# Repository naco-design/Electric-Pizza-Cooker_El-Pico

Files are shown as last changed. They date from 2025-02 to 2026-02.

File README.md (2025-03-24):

# Electric Pizza Cooker El-Pico
El-Pico, This is a programmable Electric Pizza Cooker (Oven)!
\
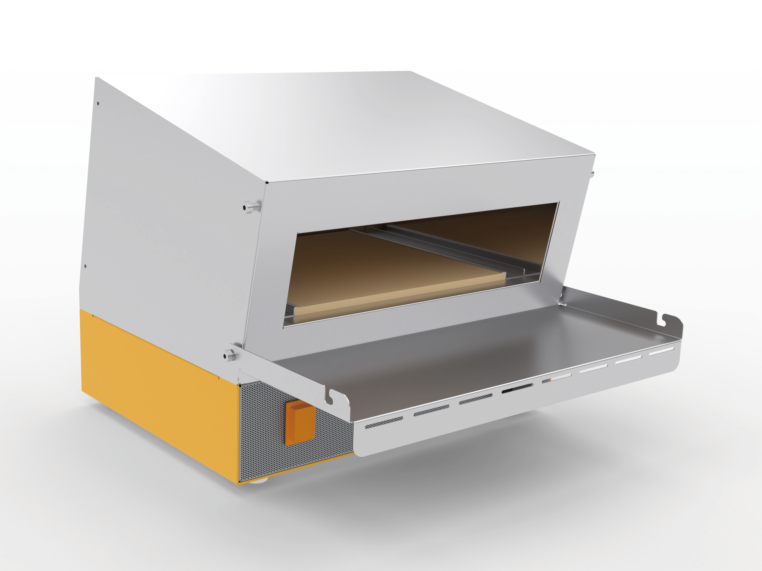
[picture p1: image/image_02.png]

CADデータのレンダリングイメージ

## Why Pizza ?
おいしいピッツァを食べたい！→ピザ窯をつくろう
\
\
以下のデータを順次公開します。
* 板金用STEPファイル
* 3Dプリント用STLファイル
* ファームウェア
* 部品のリスト
* 配線や組み立ての手順
* レシピ

## 開発にあたって
* おいしいピッツァが焼けること
* 日本の家庭用コンセントで使えること（AC100V 15A以内）
* 窯の天井485℃以上、炉床380~430℃で90秒以内で焼成可能を目指す

## 実機写真
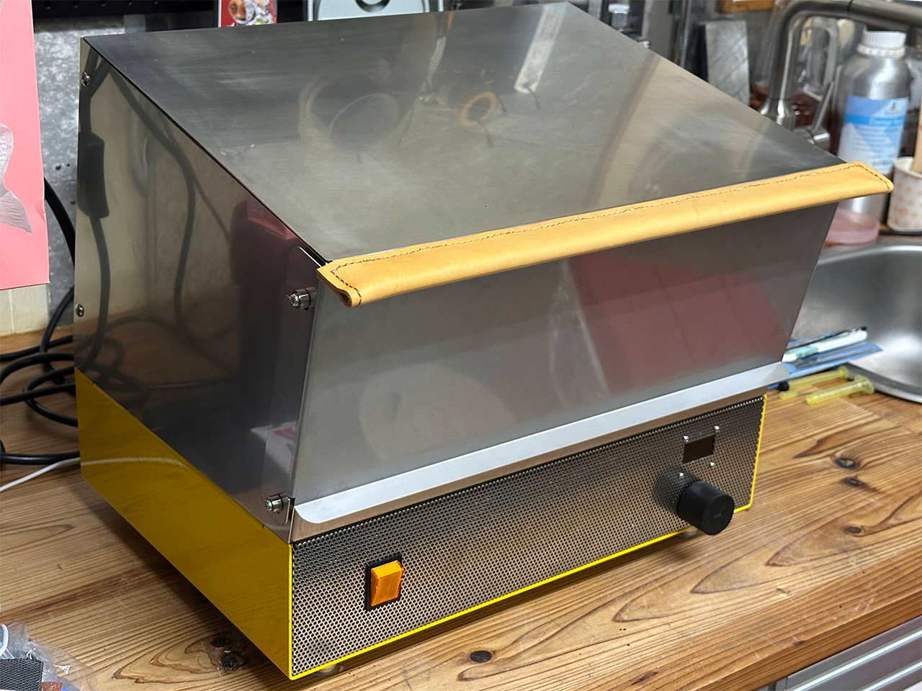
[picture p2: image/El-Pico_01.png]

天井500℃、炉床420℃の設定で90秒の焼成でおいしいピッツァを焼くことが出来ました。


2025/03/23開催のNT京都にて実機の展示
チルドピザを天井500℃、炉床370℃の設定で90秒の焼成


## コンセプト
### もっと多くの人を笑顔にしたい
開発のきっかけは、学園祭での飲食ブースの混雑と[Xの@SteveKasuya2さんのポスト](https://x.com/SteveKasuya2/status/1695339494550224910)でのオーブントースター改造ピザ窯で90 秒でピザを焼きあげる様子から、素早い提供を行えるマシンの開発に魅力を感じたことでした。
さらに、震災の報道で見た避難所の様子と[@nanbuwksさんの災害支援でピザ窯で炊き出しの記事](https://qiita.com/nanbuwks/items/adf3fea1b13d262047f9)にある支援活動の情報から、電気式のピザ窯の有用性を感じたのも理由です。

### 食は心身の健康の増進と豊かな人間形成に資する
2005 年には食育基本法が施行され、食育が現在及び将来にわたる健康で文化的な国民の生活と豊かで活力ある社会の実現に寄与するものであること、[SDGｓとも深くつながること](https://www.maff.go.jp/j/syokuiku/network/topics/2022forum.html)、また、生活の中で身近に体験する科学であり、結果をすぐに体感出来ることや新たな創意工夫を発想しやすいことから、プログラム可能なピザ窯開発を教材化しようと考えました。

### 新たな可能性は改良から生まれます。
公開するプログラムや設計を改良することで、新たな料理や素材に合わせた設定を探ったり、より良い制御を試すことが出来ます。\
筐体を作り変えたり、断熱材や蓄熱材、遮熱処理などを変更するとどうなるか、より使いやすくするためのアイデアを考えたり、MakersFair や地産地消や防災・減災イベントなどへの参加や利用も出来ると思います。

## 制作にあたって
ヒーターはとても高温（750℃程度）になります。\
特にオーブン部分は金属部品の過熱による寸法変化や変形などもあり、それらを考慮した配線の長さや部材の選定、専用工具による圧着端子での配線を行ってください。\
有資格者や同等の知識を有する方が組み立てと配線および点検を行い、事故に対応できる環境で監視のもとで使用してください。

### 設計について
まず上述のオーブントースター改造ピザ窯での情報から、TS-4119Wを購入し改造を行いデータを収集することにしました。\
数回の改良を経て満足いく性能は発揮できたものの、使い勝手の向上やサイズと外観を良くするために筐体を設計することとしました。

#### 設計の際に考慮した改善点
* ピザピールを扱いやすいように開口部の幅を広げる
* 手前と奥の焼きムラを低減する
* 制御部を下段に配置し、本体幅を抑える
* 温度設定を本体の操作で変更できるようにする

### 既知の問題点
* 熱でドアが変形し、左右のロックが片側しかかからなくなる\
→ドアの設計を変更する（設計中）

### 仕様（ プロトタイプ）
シーズヒーター * 5　合計1324W\
K 熱電対 * 4　（ヒーター * 2、プレート * 2）\
SSR * 2\
セラミック蓄熱プレート * 2\
板金部品　SUS304、A5052、SPCC（粉体塗装）\
冷却ファン、スイッチング電源

Pro Micro とMax6675 K熱電対を使用し、ヒーターをPID 制御\
リミット温度超過や熱電対断線時にはヒーター切\
ヒューズによる過電流保護\
OLED とロータリーエンコーダで温度設定を変更可能

## 公開データ
### 制作または発注する部品
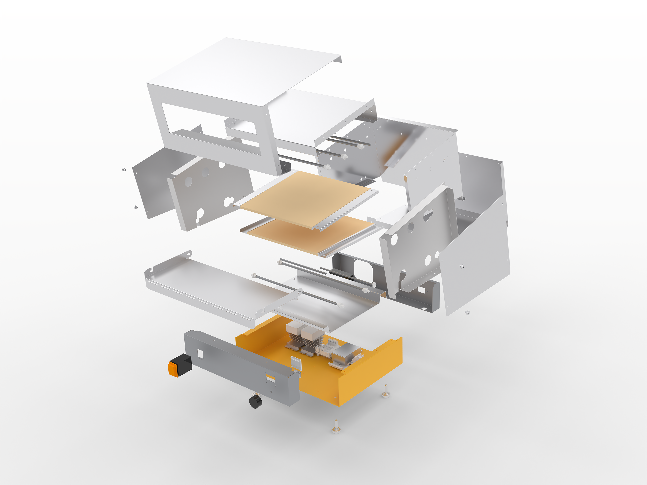
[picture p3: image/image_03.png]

[設計データ](Design)\
板金用STEPデータ\
3Dプリント用STEPデータ

### 制御プログラム
[ProMicro用ファームウェア](Firmware)\
VS Code & PlatformIOを使用します。\
TelePlotで温度やSSRへの出力値（0-255）をグラフ表示することも可能です。
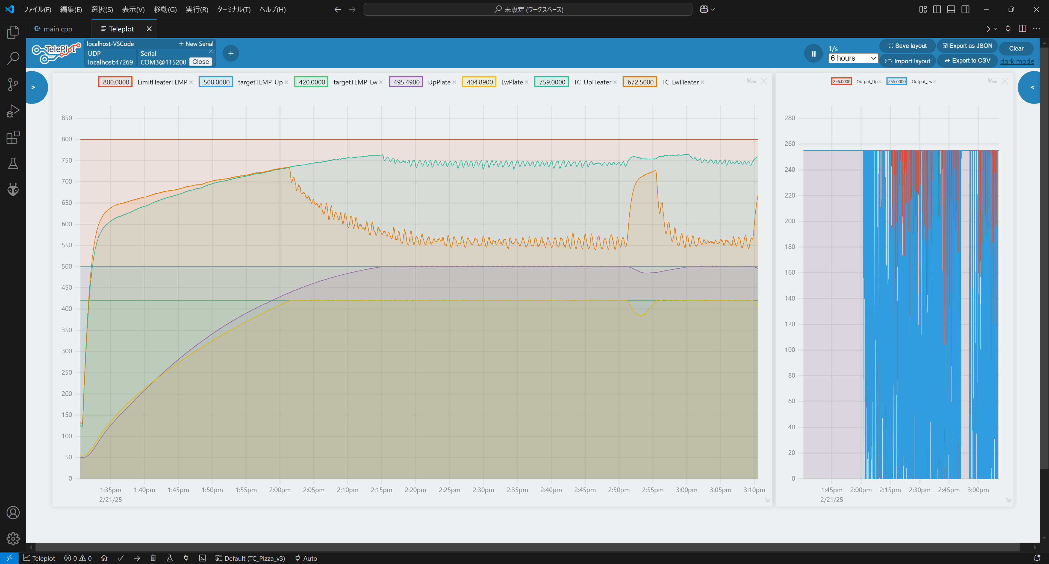
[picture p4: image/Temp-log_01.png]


### 必要部品
|部品名|型番や仕様|必要数量|参考購入先|備考|
|---|---|:-:|---|---|
シーズヒーター|345mm 315mmL 300W, 110V|3本|[AliExpress](https://ja.aliexpress.com/item/1005006249800119.html)|合計743W（100V使用時）
シーズヒーター|350mm 320mmL 350W, 110V|2本|[AliExpress](https://ja.aliexpress.com/item/1005006249800119.html)|合計581W（100V使用時）
セラミックの部品|OD9.8xH11xID6.7|10個|[AliExpress](https://ja.aliexpress.com/item/1005002340926694.html)|ヒーターと筐体の絶縁に仕様
ピザプレート|ツインバード 892009|2枚|[yodobashi](https://www.yodobashi.com/product/100000001002338272/)|TS-4119Wから流用
セラミックファイバーブランケット|厚み12.5mm|1|[MonotaRO](https://www.monotaro.com/p/2859/6829/)
アルミシート|||[Amazon](https://www.amazon.co.jp/dp/B00I7KU4JC)
耐熱電線 |15 AWG|5m|[AliExpress](https://ja.aliexpress.com/item/1005004792599537.html)
断熱編組スリーブ||1|[Amazon](https://www.amazon.co.jp/dp/B0861VLQ2J)
片サドルバンド|625-210-B|2個|[MonotaRO](https://www.monotaro.com/p/0109/6515/)
SSR||2個 |[Amazon](https://www.amazon.co.jp/dp/B0CC4VYYJ5)
SSRヒートシンク||2個|[Amazon](https://www.amazon.co.jp/dp/B0CTQBSR3H)
放熱用シリコーン||1|[Amazon](https://www.amazon.co.jp/dp/B004OQP8RQ)
Max6675 モジュール||4個|[AliExpress](https://ja.aliexpress.com/item/1005006282367831.html)
K熱電対Φ5mm|1m M8 K, 200mm|2個|[AliExpress](https://ja.aliexpress.com/item/4000097994613.html)
K熱電対Φ1mm|K 1mm, 200mm|2個|[AliExpress](https://ja.aliexpress.com/item/1005004874800021.html)
ProMicro||1|
タクトスイッチ||1|
パネルマウントUSB-C延長ケーブル ||1|[Amazon](https://www.amazon.co.jp/dp/B0887XHFML)
スイッチング電源 |ESP10-25-12|1|[MiSUMi](https://jp.misumi-ec.com/vona2/detail/110400281630/?ProductCode=ESP10-25-12)
ステンレスカラー|TCLSS4-6-10|4|[MiSUMi](https://jp.misumi-ec.com/vona2/detail/110300235050/?ProductCode=TCLSS4-6-10)
PCファン||1|[Amazon](https://www.amazon.co.jp/dp/B09M6HTSC3)
ファンガード||1|[Amazon](https://www.amazon.co.jp/gp/product/B00YH754QM)
ロッカースイッチ|A8A-216-1|1|
OLED|SSH1106 1.3 I2C|1|[Amazon](https://www.amazon.co.jp/dp/B07QC5W46K)
ヒューズホルダー||1|[MiSUMi](https://jp.misumi-ec.com/vona2/detail/222004911089/?ProductCode=FH-052S)
ガラス管ヒューズ||1|[Yodobashi](https://www.yodobashi.com/product/100000001002122484/)
圧着端子
組端子台||1|
DINレール||1|[Amazon](https://www.amazon.co.jp/dp/B076LWQCW7)
DINレール固定金具|||[Amazon](https://www.amazon.co.jp/dp/B013CXAX9Y)
電源コード||1|[Amazon](https://www.amazon.co.jp/dp/B00ID1S2W6)
インレット|C14|1|[MiSUMi](https://jp.misumi-ec.com/vona2/detail/110400165860/?ProductCode=WTN-1171AA)
電線
ステンレストラスねじ|M4-4|
ステンレストラスねじ|M4-12|
ステンレス針金
ねじ脚|MN-25M8|4|[MiSUMi](https://jp.misumi-ec.com/vona2/detail/221000121526/?ProductCode=MN-25M8)

### 必要工具
鉄鋼やすり\
+ドライバー\
ラチェット式圧着端子用工具\
はんだごて

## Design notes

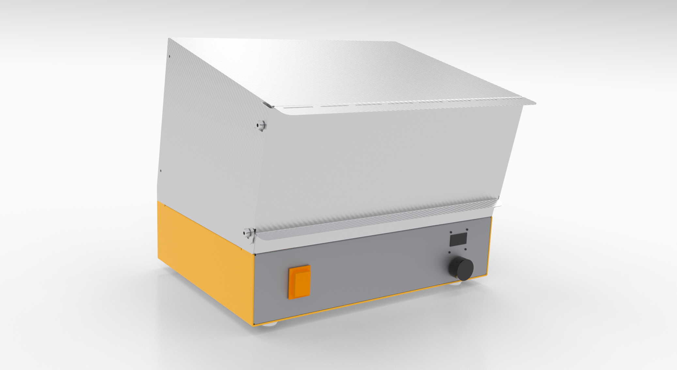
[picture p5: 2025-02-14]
image/image.png

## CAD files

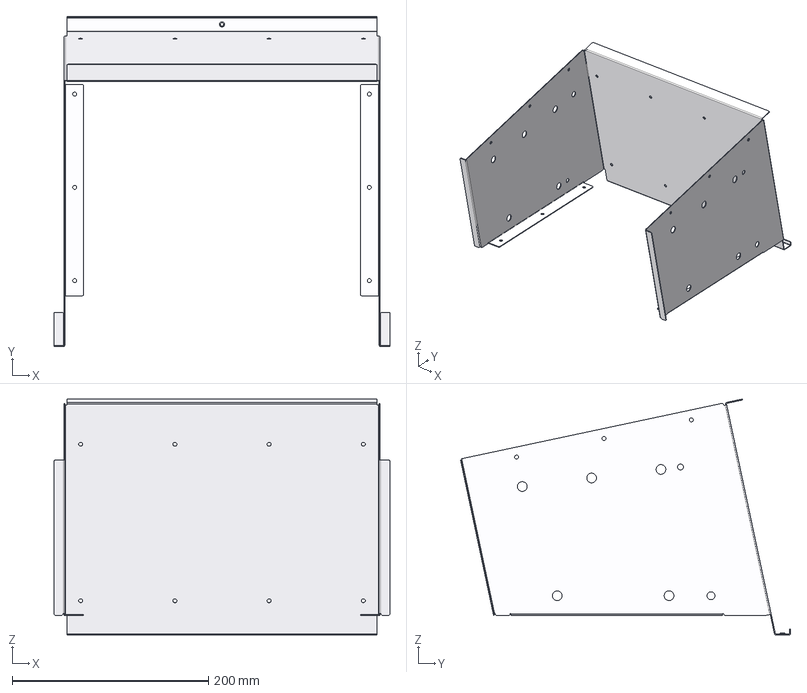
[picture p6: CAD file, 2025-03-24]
Design/v1/Oven-main.stp
342.0 x 336.1 x 240.3 mm

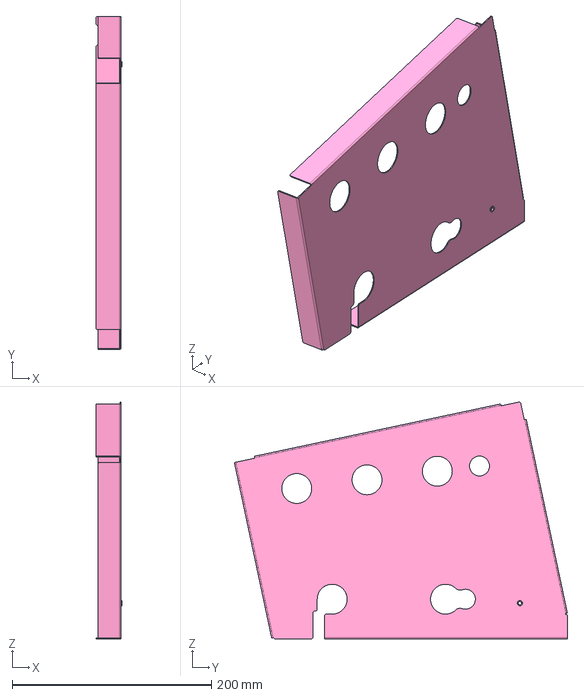
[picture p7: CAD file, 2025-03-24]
Design/v1/heat-shield-L.stp
26.0 x 334.9 x 238.1 mm

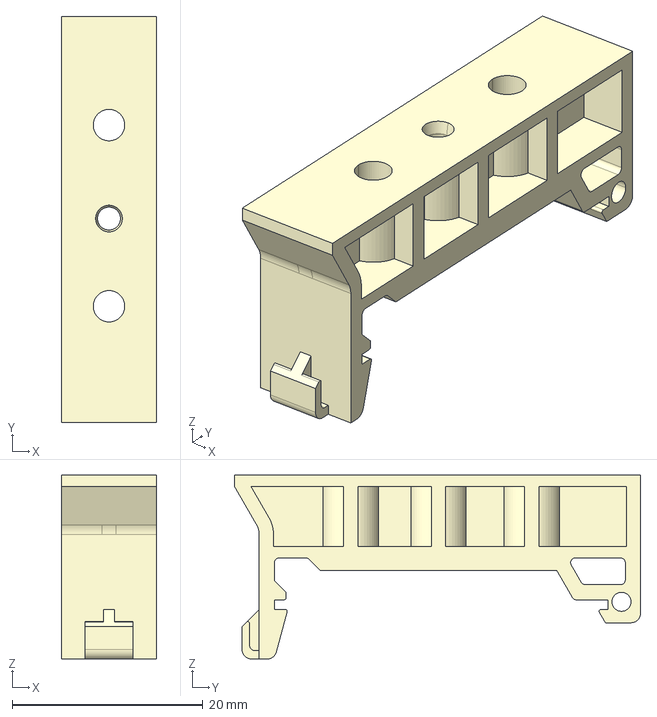
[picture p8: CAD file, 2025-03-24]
Design/v1/DIN_Holder_.stp
10.0 x 42.6 x 19.3 mm

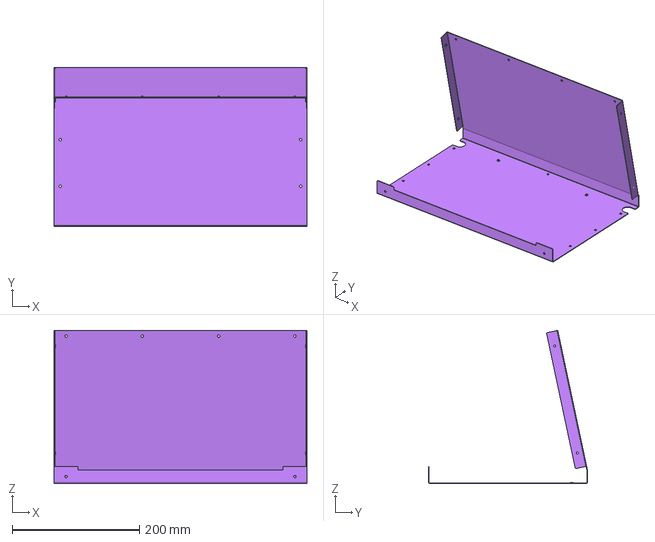
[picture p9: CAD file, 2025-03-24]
Design/v1/Outer-Back.stp
398.0 x 250.0 x 241.0 mm

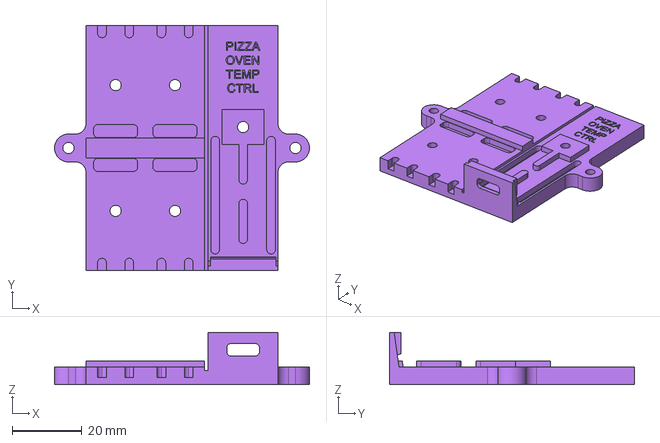
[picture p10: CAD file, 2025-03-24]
Design/v1/PiOvTeC.stp
73.0 x 70.0 x 15.0 mm

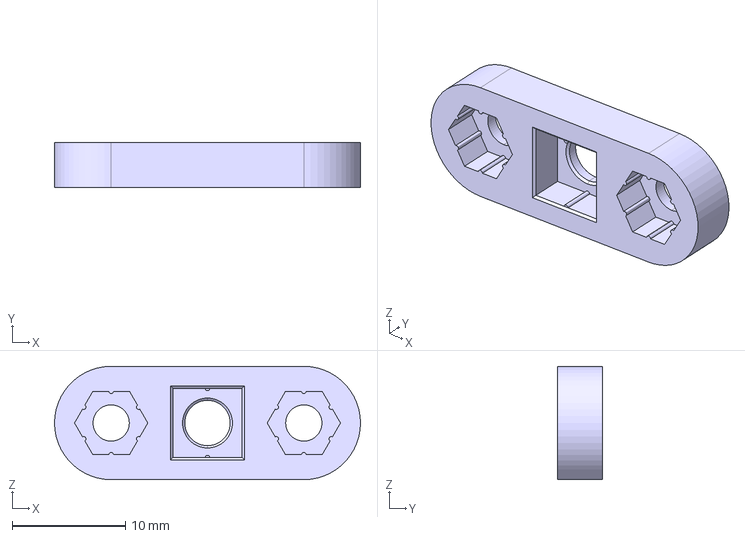
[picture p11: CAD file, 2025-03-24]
Design/v1/ResetSW_Holder.stp
27.0 x 4.00 x 10.00 mm

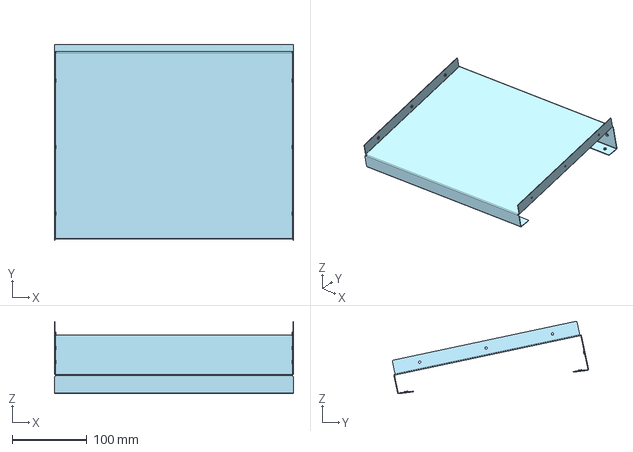
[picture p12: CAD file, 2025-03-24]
Design/v1/heat-Upper.stp
320.0 x 262.8 x 96.9 mm

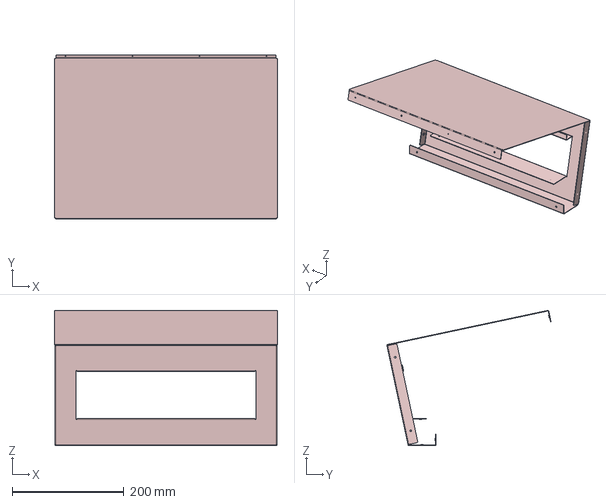
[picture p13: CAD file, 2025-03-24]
Design/v1/Outer-Front.stp
400.0 x 294.6 x 242.5 mm

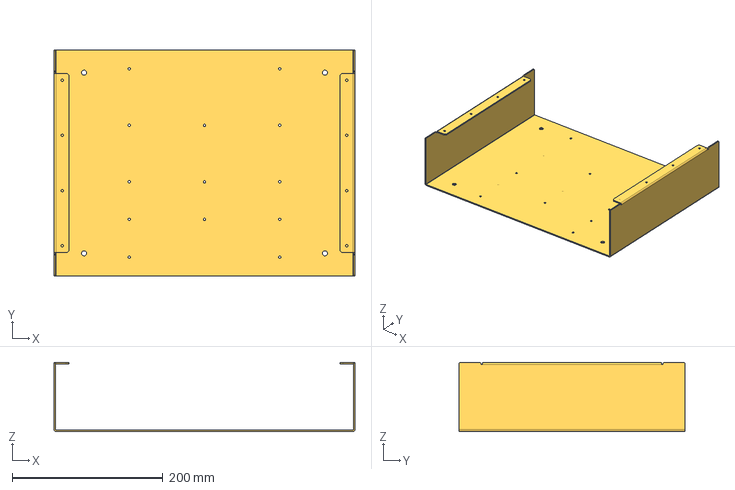
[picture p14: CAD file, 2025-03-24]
Design/v1/CtrlBox.stp
400.0 x 300.0 x 92.0 mm

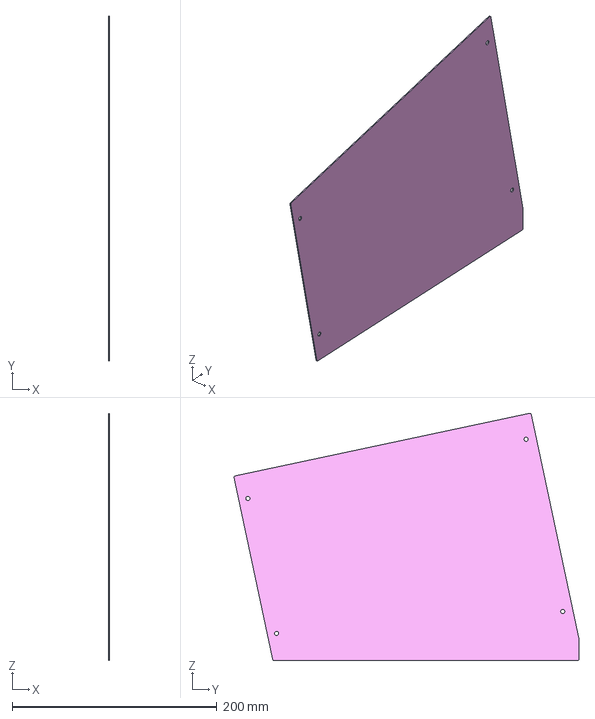
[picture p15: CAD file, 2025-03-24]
Design/v1/Outer-Side.stp
1.00 x 337.0 x 241.7 mm

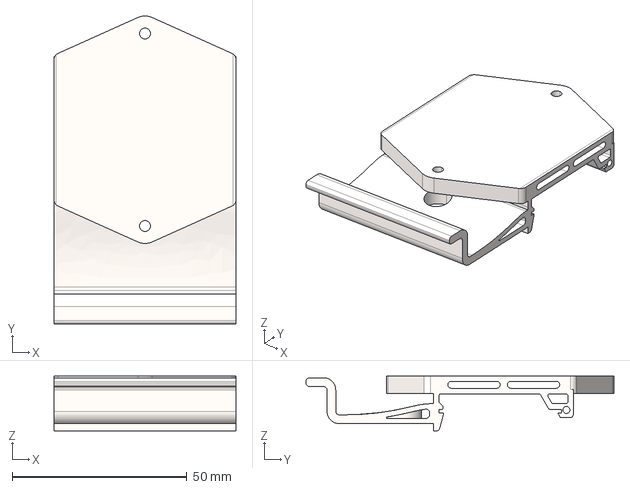
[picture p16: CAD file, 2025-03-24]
Design/v1/PowerST.stp
52.0 x 88.0 x 15.7 mm

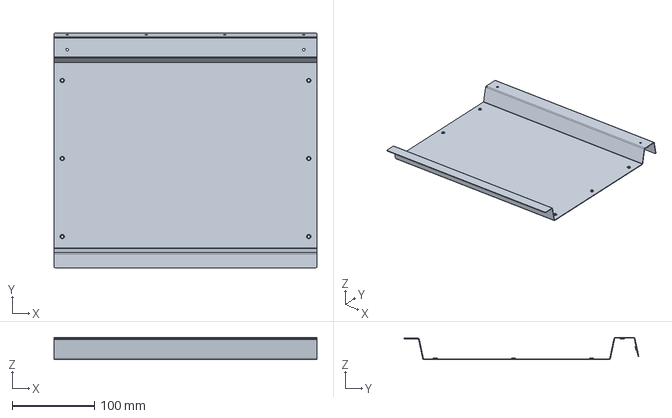
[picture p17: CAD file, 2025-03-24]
Design/v1/heat-Lower.stp
320.0 x 285.5 x 27.0 mm

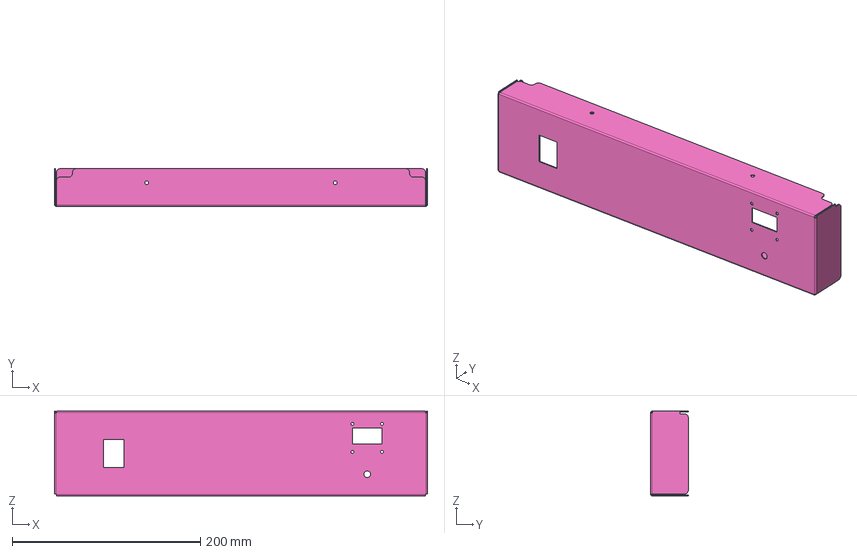
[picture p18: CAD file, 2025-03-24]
Design/v1/F-Panel.stp
396.0 x 40.0 x 90.0 mm

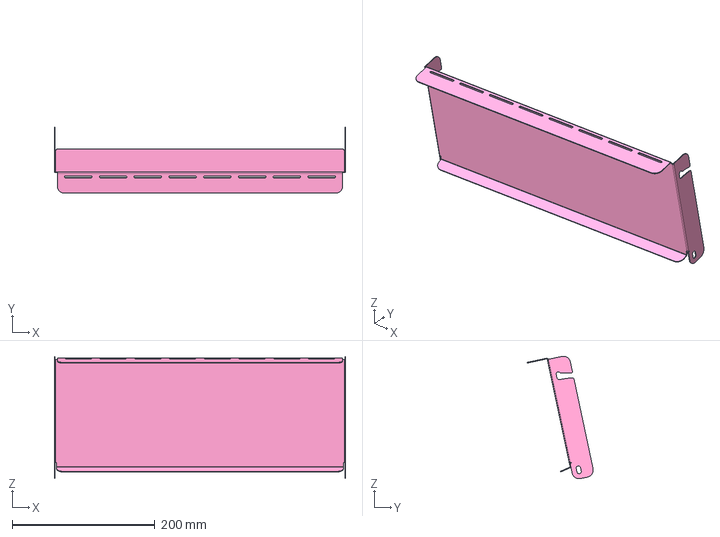
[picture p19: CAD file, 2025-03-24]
Design/v1/Door_v2.stp
408.0 x 93.2 x 171.7 mm

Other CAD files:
Design/v1/heat-shield-R.stp
Design/v1/R-Panel.stp
Design/v1/heat-Side.stp

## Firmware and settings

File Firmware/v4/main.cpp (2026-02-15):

/*********************************************************************
 * PIZZA COOKER OS v4.4
 * ---------------------------------------------------------------
 * [主要機能]
 * ・二重化熱電対によるヒーター/プレートの個別温度監視
 * ・PID制御およびオートチューニング機能
 * ・電力制限枠内での動的PWM配分（下火優先アルゴリズム）
 * ・ストーン熱浸透度（Soak）の計算と自動焼き開始判定
 *********************************************************************/

#include <Arduino.h>
#include <EEPROM.h>
#include <max6675.h>
#include <PID_AutoTune_v0.h>
#include <U8x8lib.h>
#include <avr/wdt.h>

// Arduino標準のabs(float)マクロは意図しない型変換を起こす可能性があるため、明示的なfloat版を定義
static inline float f_abs(float v) { return (v < 0.0f) ? -v : v; }

/* ================= CONFIGURATION ================= */
namespace Config {
    // EEPROMのデータ構造が変わった際に初期化を強制するための識別子
    constexpr uint32_t EEPROM_MAGIC = 0x50495A36; 

    namespace Pins {
        constexpr uint8_t THERMO_CLK   = 15, THERMO_DO = 14;
        constexpr uint8_t CS_UP_PLATE  = A1, CS_UP_HEATER  = A0; // 上火（プレート/ヒーター）
        constexpr uint8_t CS_LO_PLATE  = A3, CS_LO_HEATER  = A2; // 下火（プレート/ヒーター）
        constexpr uint8_t SSR_UP       = 5,   SSR_LO       = 6;  // PWM制御用SSR
        constexpr uint8_t SAFETY_RELAY = 9;                      // 主電源遮断用リレー
        constexpr uint8_t ENC_CLK      = 7,   ENC_DT       = 8;  // ロータリーエンコーダ
        constexpr uint8_t ENC_SW       = 4;                      // エンコーダプッシュスイッチ
    }

    namespace Hard {
        constexpr float RATED_UP_W        = 850.0f; // 上ヒーター定格
        constexpr float RATED_LO_W        = 570.0f; // 下ヒーター定格
        constexpr float STONE_THICK_MM    = 4.0f;   // ストーン厚（Soak計算に使用）
        constexpr float PLATE_MAX_C       = 650.0f; // 安全限界温度
        constexpr float HEATER_MAX_C      = 820.0f; // ヒーター損傷限界温度
        constexpr float COOL_COMPLETE_C   = 100.0f; // 冷却完了判定温度
        constexpr uint32_t RUNAWAY_TIMEOUT_MS   = 30000UL; // 暴走判定（出力0で温度上昇時）
        constexpr uint32_t REST_TIMEOUT_MS      = 30UL * 60UL * 1000UL; // 無操作自動停止
        constexpr uint32_t EEPROM_IDLE_TIMEOUT_MS = 30000UL; // 書き込み待機時間
        constexpr uint32_t BOOST_MS             = 30000UL;    // 投入直後の電力ブースト時間
        constexpr uint32_t BAKE_DONE_MSG_MS     = 3000UL;    // 完了メッセージ表示時間
        constexpr float    TUNE_TARGET_C        = 350.0f;    // オートチューニング目標
    }

    namespace Msg {
        const char PREHEAT[] PROGMEM   = "Soaking...";
        const char REST[] PROGMEM      = "I'll be back";
        const char COOL[] PROGMEM      = "I'll be cool";
        const char DONE[] PROGMEM      = "Well done. Ciao!";
        const char ERROR[] PROGMEM     = "Safety Stop";
        const char BAKE_DONE[] PROGMEM = "Buon appetito!";
    }

#pragma pack(push, 1) // メモリ節約のためパディングを禁止
    struct Recipe {
        char name[8];
        float upC, loC;      // 目標温度
        char readyMsg[22];   // 到達時メッセージ
        uint16_t bakeSec;    // 標準焼き時間
    };
#pragma pack(pop)

    const Recipe recipes[] PROGMEM = {
        {"Napoli", 500.0f, 430.0f, "Pizza Time",     90},
        {"Romana", 330.0f, 310.0f, "Crispy Romana", 180}
    };
    constexpr uint8_t RECIPE_CNT = sizeof(recipes) / sizeof(Recipe);

    struct Limit { char label[6]; float watts; };
    const Limit limits[] PROGMEM = {
        {"1.4kW", 1420.0f}, // 15Aコンセント許容範囲
        {"1.0kW", 1000.0f},
        {"0.7kW",  700.0f}
    };
    constexpr uint8_t LIMIT_CNT = sizeof(limits) / sizeof(Limit);
}

namespace AskConfirmation {
    constexpr uint8_t NONE = 0;
    constexpr uint8_t CANCEL_TUNE = 1;
    constexpr uint8_t START_TUNE = 2;
    constexpr uint8_t FACTORY_RESET = 3;
}

/* ================= HEATER CONTROL CLASS ================= */
// 1つのヒーターユニット（プレート+ヒーターの2個のセンサー）を管理するクラス
class IntelligentHeater {
public:
    float plateC = 0, heaterC = 0, soak = 0, trend = 0;
    uint8_t pwm = 0, error = 0; // error bit: 0:Sensor, 1:Runaway, 2:Overheat

    IntelligentHeater(uint8_t csP, uint8_t csH, uint8_t ssr)
        : _plate(Config::Pins::THERMO_CLK, csP, Config::Pins::THERMO_DO),
          _heater(Config::Pins::THERMO_CLK, csH, Config::Pins::THERMO_DO),
          _ssr(ssr) {
        pinMode(_ssr, OUTPUT);
        digitalWrite(_ssr, LOW);
        _winStart = millis();
    }

    // 制御サイクルの実行（毎秒呼び出し）
    // インライン展開を防ぎFlashを節約
    bool tick(float target, float &health) __attribute__((noinline)) {
        float rp = _plate.readCelsius(), rh = _heater.readCelsius();

        // [異常検知] センサーエラー時は即座にPWMを0にし、SSRを物理的に停止
        if (isnan(rp) || rp < 0.0f || rp > Config::Hard::PLATE_MAX_C || // プレートセンサーの異常値
            isnan(rh) || rh < 0.0f || rh > Config::Hard::HEATER_MAX_C + 100.0f) { // ヒーターセンサーの異常値
            error |= 1; pwm = 0; _out = 0; digitalWrite(_ssr, LOW); return false;
        }
        error &= ~1;
        heaterC = rh;

        // 初回起動時の温度追従
        if (_first) { 
            plateC = rp; _first = false; _runawayMs = millis(); 
            _lastInput = plateC;
        }

        // [フィルタリング] 温度変化を平滑化
        float prev = plateC;
        plateC = 0.8f * plateC + 0.2f * rp;
        trend = 0.9f * trend + 0.1f * (plateC - prev); // 温度勾配（トレンド）を算出

        // [Soak計算] ストーンの芯まで熱が通ったかをシミュレート
        float step = 1.0f / Config::Hard::STONE_THICK_MM;
        if (target > 50.0f && f_abs(target - plateC) < 5.0f)
            soak = min(100.0f, soak + step); // 目標付近なら浸透
        else
            soak = max(0.0f, soak - step * 0.5f); // 離れていれば放熱

        _in  = plateC;
        _set = target;

        // PID演算またはオートチューニングの実行
        if (_tuning) {
            if (_aTune && _aTune->Runtime() != 0) {
                setTunings(_aTune->GetKp(), _aTune->GetKi(), _aTune->GetKd());
                stopTune(); // チューニング完了処理（メモリ解放含む）
            }
        } else {
            // 簡易PID計算 (float統一でコードサイズ削減)
            float error = _set - _in;
            _iTerm += (_ki * error);
            if (_iTerm > 255.0f) _iTerm = 255.0f; else if (_iTerm < 0.0f) _iTerm = 0.0f;
            
            float dInput = (_in - _lastInput);
            float output = _kp * error + _iTerm - _kd * dInput;
            
            if (output > 255.0f) output = 255.0f; else if (output < 0.0f) output = 0.0f;
            _out = output;
            _lastInput = _in;
        }
        pwm = static_cast<uint8_t>(_out);

        // [暴走検知] 出力0なのに急激に温度が上がっている場合はSSRの短絡を疑う
        uint32_t now = millis();
        if (pwm == 0 && trend > 1.5f) {
            if (now - _runawayMs > Config::Hard::RUNAWAY_TIMEOUT_MS) error |= 2;
        } else {
            _runawayMs = now;
        }

        // [健康度/過昇温管理] ヒーターフィラメントのダメージを累積計算
        float limit = Config::Hard::HEATER_MAX_C;
        bool damaged = false;
        if (heaterC > limit + 40.0f) {
            health = max(0.0f, health - 0.01f);
            damaged = true;
        } else if (heaterC > limit + 20.0f) {
            health = max(0.0f, health - 0.002f);
            damaged = true;
        }

        if (plateC > Config::Hard::PLATE_MAX_C) error |= 4;
        return damaged;
    }

    // SSRのタイムプロポーショニング制御（1秒周期内でのON時間を制御）
    void drive(uint8_t out) {
        if (out != _lastOut) {
            _onTimeMs = static_cast<uint32_t>(out) * 1000 / 255;
            _lastOut = out;
        }
        uint32_t now = millis();
        if (now - _winStart >= 1000UL) _winStart = now;
        digitalWrite(_ssr, (now - _winStart < _onTimeMs) ? HIGH : LOW);
    }

    // エラーや状態遷移時のリセット処理
    void reset() { 
        error = 0; pwm = 0; _out = 0; soak = 0; trend = 0; _overheatCnt = 0;
        _first = true; digitalWrite(_ssr, LOW);
        plateC = 0; heaterC = 0;
        _runawayMs = millis(); _winStart = millis();
        _iTerm = 0; _lastInput = 0; // PID内部変数のリセット
    }
    
    float pidOut() const { return _out; }
    void setTunings(float kp, float ki, float kd) { _kp = kp; _ki = ki; _kd = kd; }
    float getKp() { return _kp; }
    float getKi() { return _ki; }
    float getKd() { return _kd; }

    void startTune() {
        if (_aTune) delete _aTune; // 念のため既存があれば削除
        _aTune = new PID_ATune((double*)&_in, (double*)&_out);
        _tuning = true;
        _aTune->SetNoiseBand(2);
        _aTune->SetOutputStep(255);
        _aTune->SetLookbackSec(12);
        _aTune->SetControlType(1);
    }
    void stopTune() { _tuning = false; if (_aTune) { delete _aTune; _aTune = nullptr; } }
    bool isTuning() const { return _tuning; }

private:
    MAX6675 _plate, _heater;
    PID_ATune* _aTune = nullptr; // メモリ節約のためポインタに戻す
    uint8_t _ssr;
    float  _in, _out, _set;
    uint32_t _runawayMs = 0, _winStart = 0;
    bool     _first = true, _tuning = false;
    uint8_t _overheatCnt = 0;
    uint16_t _lastOut = 256; // キャッシュ用（初期値は範囲外）
    uint32_t _onTimeMs = 0;
    float _kp = 3.5f, _ki = 0.05f, _kd = 1.0f;
    float _iTerm = 0.0f, _lastInput = 0.0f;
};

/* ================= GLOBALS ================= */
IntelligentHeater up(Config::Pins::CS_UP_PLATE, Config::Pins::CS_UP_HEATER, Config::Pins::SSR_UP);
IntelligentHeater lo(Config::Pins::CS_LO_PLATE, Config::Pins::CS_LO_HEATER, Config::Pins::SSR_LO);
// U8x8モード（バッファレス・高速・省メモリ）で初期化
U8X8_SH1106_128X64_NONAME_HW_I2C oled(/* reset=*/ U8X8_PIN_NONE);

enum class OvenState : uint8_t { IDLE, PREHEAT, READY, BAKING, BAKE_DONE, REST, COOLING, SHUTDOWN, ERROR, TUNING };
OvenState oven = OvenState::IDLE, prevOven = OvenState::IDLE;

#pragma pack(push, 1)
struct Settings { 
    uint32_t magic; uint8_t recipeIdx, limitIdx; float upHealth, loHealth; 
    float upKp, upKi, upKd;
    float loKp, loKi, loKd;
} settings;
Settings lastSaveSettings; // EEPROMに保存されている値のシャドウコピー
#pragma pack(pop)

bool baking = false;
uint8_t askConfirmation = AskConfirmation::NONE; // 現在表示中の確認プロンプトID
bool confirmationYes = false;              // プロンプトでの選択状態 (Y/N)
uint8_t tuneStage = 0;                     // オートチューニングの進行状況
uint16_t curBakeSec = 0;
uint32_t bakeStartMs = 0, bakeDoneMsgMs = 0, boostStartMs = 0, restStartMs = 0, lastActMs = 0;
float lastSavedUpHealth = 100.0f;
float lastSavedLoHealth = 100.0f;
Config::Recipe currentRecipe; // 現在のレシピを保持するキャッシュ
uint8_t targetUpPWM = 0, targetLoPWM = 0; // 計算済みのPWM値

const __FlashStringHelper* temporaryMsg = nullptr;
uint32_t temporaryMsgEndMs = 0;

// EEPROMへの遅延書き込み処理（頻繁な書き込みによる寿命低下を防止）
void dirtySave(bool set = false) {
    static bool dirty = false; static uint32_t lastMs = 0;
    if (set) { dirty = true; lastMs = millis(); return; }
    
    // タイムアウト経過、または即時保存が必要なステート（SHUTDOWN/ERROR）の場合
    bool timeout = (millis() - lastMs > Config::Hard::EEPROM_IDLE_TIMEOUT_MS);
    bool urgent = (oven == OvenState::SHUTDOWN || oven == OvenState::ERROR);

    if (dirty && (timeout || urgent)) {
        dirty = false;
        // 実際に値が変更されている場合のみ書き込み（RAM上のシャドウコピーと比較）
        if (memcmp(&settings, &lastSaveSettings, sizeof(Settings)) != 0) {
            EEPROM.put(0, settings);
            lastSaveSettings = settings;
        }
    }
}

void startBake(uint16_t sec) {
    baking = true; curBakeSec = sec;
    bakeStartMs = boostStartMs = lastActMs = millis();
    oven = OvenState::BAKING;
}

// エンコーダとスイッチのデバウンス処理付き入力管理
void handleInput(uint32_t now) {
    static int lastClk = HIGH; 
    static uint32_t lastEncMs = 0;
    int clk = digitalRead(Config::Pins::ENC_CLK);

    if (lastClk == HIGH && clk == LOW && now - lastEncMs > 50UL) {
        lastEncMs = now;
        lastActMs = now;
        int dir = (digitalRead(Config::Pins::ENC_DT) != LOW) ? 1 : -1;
        if (askConfirmation != AskConfirmation::NONE) {
            confirmationYes = !confirmationYes; // Y/N 切り替え
        } else if (oven != OvenState::ERROR && oven != OvenState::TUNING) {
            settings.recipeIdx = (settings.recipeIdx + dir + Config::RECIPE_CNT) % Config::RECIPE_CNT;
            memcpy_P(&currentRecipe, &Config::recipes[settings.recipeIdx], sizeof(currentRecipe));
            dirtySave(true);
        }
    }
    lastClk = clk;

    static bool lastSw = HIGH;
    static uint32_t pressStartMs = 0;
    static bool longPressHandled = false;
    const uint32_t LONG_PRESS_MS = 2000UL;
    const uint32_t DEBOUNCE_MS = 50UL;

    bool sw = digitalRead(Config::Pins::ENC_SW);

    if (sw == LOW && lastSw == HIGH) { // Button just pressed
        pressStartMs = now;
        longPressHandled = false;
    } else if (sw == HIGH && lastSw == LOW) { // Button just released
        if (now - pressStartMs > DEBOUNCE_MS && !longPressHandled) {
            // Short press action
            lastActMs = now;
            if (askConfirmation != AskConfirmation::NONE) {
                if (confirmationYes) {
                    // [汎用] 選択されたアクションの実行
                    if (askConfirmation == AskConfirmation::CANCEL_TUNE) {
                        up.stopTune(); lo.stopTune();
                        up.reset(); lo.reset();
                        oven = OvenState::SHUTDOWN;
                        tuneStage = 0; // 進行状況をリセット
                        temporaryMsg = F("Canceled");
                        temporaryMsgEndMs = now + 2000UL;
                        dirtySave(true);
                    } else if (askConfirmation == AskConfirmation::START_TUNE) {
                        up.reset(); lo.reset();
                        oven = OvenState::TUNING;
                        tuneStage = 0;
                        temporaryMsg = F("Tuning Start");
                        temporaryMsgEndMs = now + 2000UL;
                    } else if (askConfirmation == AskConfirmation::FACTORY_RESET) {
                        // デフォルト値の設定と保存
                        settings = {
                            Config::EEPROM_MAGIC, 0, 0, 100.0f, 100.0f, 
                            3.5f, 0.05f, 1.0f, 
                            3.5f, 0.05f, 1.0f
                        };
                        EEPROM.put(0, settings);
                        lastSaveSettings = settings;
                        // 設定を即時反映
                        up.setTunings(settings.upKp, settings.upKi, settings.upKd);
                        lo.setTunings(settings.loKp, settings.loKi, settings.loKd);
                        memcpy_P(&currentRecipe, &Config::recipes[settings.recipeIdx], sizeof(currentRecipe));
                        
                        up.reset(); lo.reset();
                        oven = OvenState::SHUTDOWN;
                        
                        temporaryMsg = F("Factory Reset");
                        temporaryMsgEndMs = now + 2000UL;
                    }
                }
                askConfirmation = AskConfirmation::NONE; // プロンプトを閉じる
            } else if (oven != OvenState::ERROR && oven != OvenState::TUNING) {
                settings.limitIdx = (settings.limitIdx + 1) % Config::LIMIT_CNT;
                dirtySave(true);
            }
        }
    } else if (sw == LOW && !longPressHandled) { // Button is being held down
        if (now - pressStartMs > LONG_PRESS_MS) {
            // Long press action
            lastActMs = now;
            if (oven == OvenState::TUNING) {
                askConfirmation = AskConfirmation::CANCEL_TUNE; // キャンセルメニュー表示
                confirmationYes = false; // デフォルトはNo
                longPressHandled = true;
            } else if (oven == OvenState::ERROR) {
                oven = OvenState::IDLE;
                digitalWrite(Config::Pins::SAFETY_RELAY, HIGH);
                temporaryMsg = F("System Reset");
                temporaryMsgEndMs = now + 1000UL;
            } else if (oven == OvenState::IDLE) {
                askConfirmation = AskConfirmation::FACTORY_RESET;
                confirmationYes = false;
            }
            longPressHandled = true;
        }
    }
    lastSw = sw;
}

// 全体電力を制限枠内に収めるための動的PWM制限アルゴリズム
void calculatePower(uint32_t now) {
    if (oven == OvenState::TUNING) {
        targetUpPWM = static_cast<uint8_t>(up.pidOut());
        targetLoPWM = static_cast<uint8_t>(lo.pidOut());
        return;
    }
    
    // 浮動小数点演算を回避し、整数演算(int32_t)で処理することで高速化
    Config::Limit lim;
    memcpy_P(&lim, &Config::limits[settings.limitIdx], sizeof(lim));
    int32_t limW = static_cast<int32_t>(lim.watts);
    int32_t ratedUp = static_cast<int32_t>(Config::Hard::RATED_UP_W);
    int32_t ratedLo = static_cast<int32_t>(Config::Hard::RATED_LO_W);

    // Boostモード: 生地の投入による下火の低下を防ぐため、下火に優先的に電力を割り当てる
    if (baking && now - boostStartMs < Config::Hard::BOOST_MS) {
        int32_t upReqW = (static_cast<int32_t>(up.pidOut()) * ratedUp) / 255;
        int32_t loReqW = (static_cast<int32_t>(lo.pidOut()) * ratedLo) / 255;

        int32_t loActiveW = (limW < loReqW) ? limW : loReqW; 
        int32_t upMaxW = (limW - loActiveW > 0) ? (limW - loActiveW) : 0;

        int32_t upAllocW = (upReqW < upMaxW) ? upReqW : upMaxW;
        targetUpPWM = static_cast<uint8_t>((upAllocW * 255) / ratedUp);
        targetLoPWM = static_cast<uint8_t>((loActiveW * 255) / ratedLo);
    } else {
        // 通常時: 下火を最優先し、残りの電力枠を上火に提供
        int32_t loReqW = (static_cast<int32_t>(lo.pidOut()) * ratedLo) / 255;
        int32_t loW = (loReqW < limW) ? loReqW : limW;
        
        int32_t remW = (limW - loW > 0) ? (limW - loW) : 0;
        int32_t upReqW = (static_cast<int32_t>(up.pidOut()) * ratedUp) / 255;
        int32_t upW = (upReqW < remW) ? upReqW : remW;

        targetUpPWM = static_cast<uint8_t>((upW * 255) / ratedUp);
        targetLoPWM = static_cast<uint8_t>((loW * 255) / ratedLo);
    }
    
    // 重大なエラーが発生している場合は出力を強制遮断
    if (up.error || lo.error || oven == OvenState::ERROR) { targetUpPWM = targetLoPWM = 0; }
}

void renderOLED() {
    // oled.clear(); // 削除：点滅防止のため

    oled.setFont(u8x8_font_chroma48medium8_r); 

    // 1行目：レシピ名と電力制限 (上書き用に空白を付加)
    oled.setCursor(0, 0); oled.print(currentRecipe.name);
    oled.print(F("        ")); // 古い名前を消すための空白
    oled.setCursor(11, 0);
    char limitLabel[6];
    strcpy_P(limitLabel, Config::limits[settings.limitIdx].label);
    oled.print(limitLabel);
    
    // 2-3行目：温度 (2x2倍角)
    // Uは0列、Lは8列から開始。2x2なので行2と行3を占有します。
    oled.setFont(u8x8_font_px437wyse700b_2x2_r);
    oled.setCursor(0, 2); oled.print(F("U")); oled.print((int)up.plateC);
    oled.print(F(" ")); // 桁数が減った時のゴミ消し
    
    oled.setCursor(8, 2); oled.print(F("L")); oled.print((int)lo.plateC);
    oled.print(F(" "));
    
    oled.setFont(u8x8_font_chroma48medium8_r); 

    // 4行目：Soak と 警告
    // 警告は温度のすぐ下（行4）に配置
    oled.setCursor(0, 4);
    if (settings.upHealth < 20.0f || settings.loHealth < 20.0f) {
        oled.print(F("!! MAINT !! ")); 
    } else {
        oled.print(F("            ")); // 警告が消えた時にクリア
    }
    
    oled.setCursor(12, 4); 
    int sk = (int)min(up.soak, lo.soak);
    if(sk < 100) oled.print(F(" ")); // 桁揃え
    oled.print(sk); oled.print(F("%"));

    // 5-6行目：焼き時間
    oled.setCursor(0, 5);
    if (oven == OvenState::BAKING) {
        int32_t rem = static_cast<int32_t>(curBakeSec) - static_cast<int32_t>((millis() - bakeStartMs) / 1000);
        oled.print(F("Bake: ")); oled.print(max(0L, rem)); oled.print(F("s  "));
    } else {
        oled.print(F("                ")); // 非表示時にクリア
    }
    
    // 7行目：ステータス (最下段)
    oled.setCursor(0, 7);
    char buf[17];
    const char* src = nullptr;
    bool isProgmem = false;
    
    if (temporaryMsg != nullptr && millis() < temporaryMsgEndMs) {
        src = (const char*)temporaryMsg; isProgmem = true;
    } else if (askConfirmation != AskConfirmation::NONE) {
        // [汎用] プロンプト表示の構築
        const char* title = (askConfirmation == AskConfirmation::CANCEL_TUNE) ? "Cancel?" : 
                            (askConfirmation == AskConfirmation::START_TUNE) ? "Tune?" : 
                            (askConfirmation == AskConfirmation::FACTORY_RESET) ? "Reset?" : "Sure?";
        strcpy(buf, title); strcat(buf, confirmationYes ? " [Y] N" : " Y [N]");
    } else {
        temporaryMsg = nullptr;
        switch (oven) {
            case OvenState::PREHEAT:   src = Config::Msg::PREHEAT; isProgmem = true; break;
            case OvenState::READY:     src = currentRecipe.readyMsg; isProgmem = false; break;
            case OvenState::BAKING:    src = "Baking..."; isProgmem = false; break;
            case OvenState::BAKE_DONE: src = Config::Msg::BAKE_DONE; isProgmem = true; break;
            case OvenState::REST:      src = Config::Msg::REST; isProgmem = true; break;
            case OvenState::COOLING:   src = Config::Msg::COOL; isProgmem = true; break;
            case OvenState::ERROR:     src = Config::Msg::ERROR; isProgmem = true; break;
            case OvenState::TUNING:    src = "Auto Tuning..."; isProgmem = false; break;
            default: break;
        }
    }
    
    // バッファへのコピーとパディングを1パスで実行（memset/strncpyのオーバーヘッド削減）
    size_t i = 0;
    if (src) {
        while (i < 16) {
            char c = isProgmem ? pgm_read_byte(src + i) : src[i];
            if (c == '\0') break;
            buf[i++] = c;
        }
    } else if (askConfirmation != AskConfirmation::NONE) {
        i = strlen(buf); // bufは既に埋まっている
    }
    while (i < 16) buf[i++] = ' ';
    buf[16] = '\0';
    oled.print(buf);
}

void updateDisplay(uint32_t now) {
    static uint32_t lastOledMs = 0;
    // Flash節約のため、部分更新ロジックを廃止し、単純な定期更新に戻す
    // 1秒経過、またはオーブンの状態（IDLE/BAKING等）が変わった時のみ再描画
    if (oven != prevOven || now - lastOledMs >= 1000UL) {
        renderOLED();
        prevOven = oven;
        lastOledMs = now;
    }
}
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
void loop() {
    wdt_reset(); 
    uint32_t now = millis();
    
    handleInput(now);
    runControlTick(now);

    if (oven == OvenState::ERROR) {
        up.drive(0);
        lo.drive(0);
    } else {
        if (oven == OvenState::TUNING && tuneStage == 1) targetLoPWM = 0;
        if (oven == OvenState::TUNING && tuneStage == 3) targetUpPWM = 0;
        up.drive(targetUpPWM); lo.drive(targetLoPWM);
    }

    updateDisplay(now);
    dirtySave(); // 必要に応じて保存実行
    debugTelemetry(now);
}
